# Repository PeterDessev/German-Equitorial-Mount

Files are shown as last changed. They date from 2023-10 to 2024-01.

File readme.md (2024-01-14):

# GEM Driver

An (almost) fully open source German Equitorial Mount currently under development. Publishing of step files for the GEM is under way. The project is based on the Arduino Nano and uses a TMC2209 stepper driver. Amost all parts are either fully 3D-Printable or standard hardware such as metric screws and steel rods.

## Building

Before building initialize and update git submodules, if not already done, with

```zsh
git submodule init
git submodule update
```

Bulding has been tested on Arch linux. To build, run the following.

```zsh
bash quickUpload.sh PORT
```

Where PORT is the arudino's UART port. On linux this is usually `/dev/ttyUSB#`, on windows `com#`.

## TMC Stepper

The main driver of the GEM is a TMC2209 configured over UART. The [TMCStepper library](https://github.com/teemuatlut/TMCStepper/tree/master) was used in the development of the driver, however was stripped down and modified to be more compatable with pure AVR-C, and less reliant on Arduino and the Arduino library. In the future, I would like to completely remove all dependancy on the Arduino Library to simplify building and development.

## Schematic

The schematic was made and can be edited using [KiCad](https://www.kicad.org/). A PCB does not exist yet but is in the works

## Mechanics

Currently the driver is mechanically driven with a NEMA 17 stepper motor mounted on a 100:1 gearbox, though this will be reduced to at least a 25:1 in the future. A 2GT timing belt and two timing pulleys are also used. While printing the pulleys is possible, it is recomended to purchase these to reduce the eccentricity in the drive mechanism, which leads to poor tracking.

### The Worm

The GEM requires a worm gear to drive the tracking mechanism. Printing a worm gear is "possible" depending on the quality of the printer used, however, in most cases it is both easier and produces better results to use a purchased brass worm. In either case, the worm should have a modulus of 0.5 and a bore of at least 6mm to prevent accedentally bending the shaft during assembly or usage. Such worms can be found relativly easily on the internet for around $15, and sometimes come with an accompanying worm drive, which most likely will not be of much use.

## Optics

The GEM also requires a polar scope, which is friction fitted into the gem. The polar scope is the same one used in the SkyWatcher EQ-5, and probably many other mounts, for which replacement parts exist in the usual places on the internet, usually under $100 (I purchased mine off of Amazon for ~$35). Though the polar scope may not be strictly nescessary, since the GEM is much more likely to be limited by the accuracy of the drive mechanism, it makes polar alignment significantly easier, and removes one step in debugging tracking problems.

## Next Steps

Development of the project is planned to continue. Here are the major tasks that still need to be completed, in no particular order:

 - [x] Release CAD files
 - [ ] Move from Atmega to STM32
 - [ ] Create PCB
 - [ ] Add BOM
 - [ ] Create Assembly Instructions
 - [x] Remove Arduino dependancy
 - [x] Release electronics schematic
 - [x] Clean project repo
 - [x] Migrate to a real build system

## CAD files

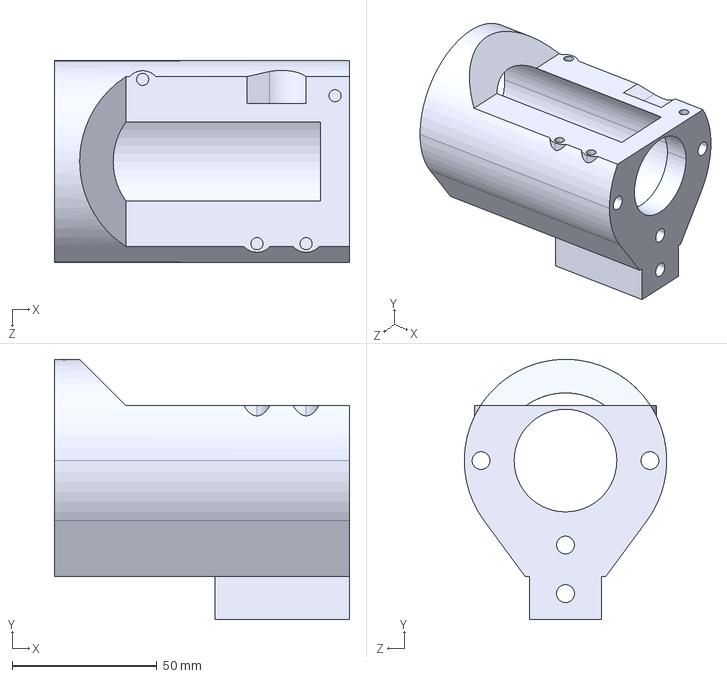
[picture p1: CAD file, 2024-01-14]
cadFiles/step/roll housing.step
102.0 x 90.0 x 70.0 mm

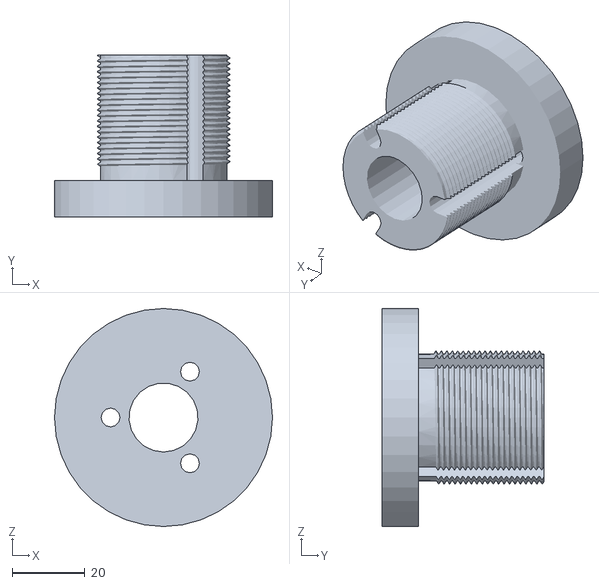
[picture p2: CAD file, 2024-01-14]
cadFiles/stl/roll face slip.STL
60.0 x 44.5 x 60.0

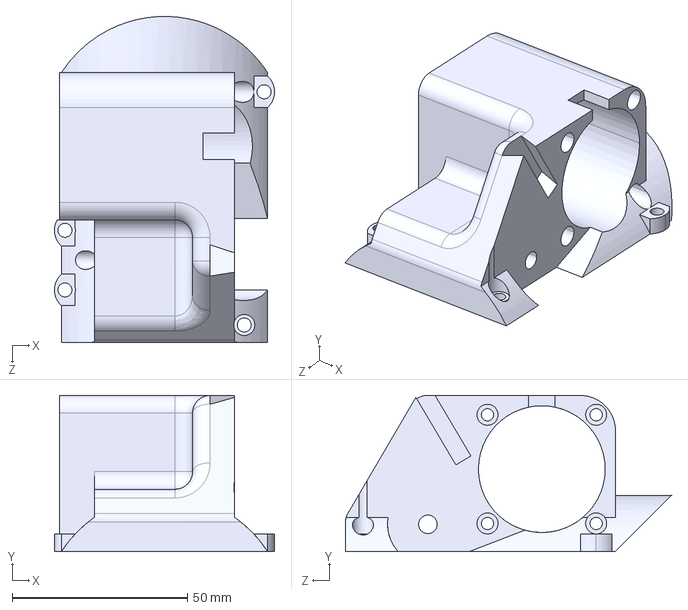
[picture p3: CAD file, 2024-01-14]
cadFiles/step/bridge.step
62.8 x 44.5 x 93.0 mm

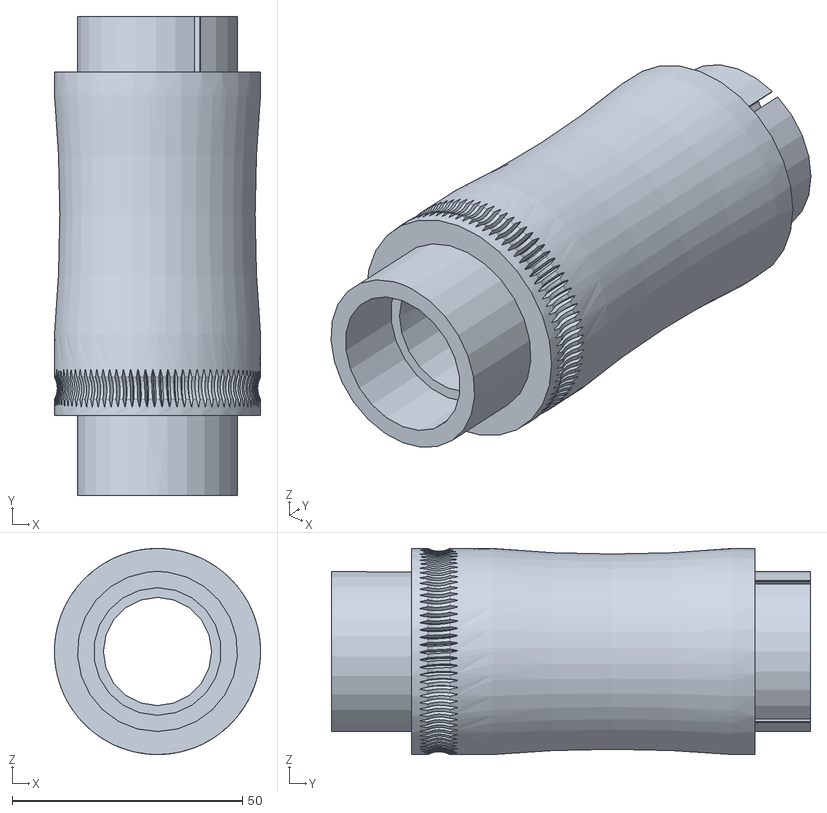
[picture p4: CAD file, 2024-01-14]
cadFiles/stl/roll body.STL
44.8 x 104.0 x 44.8

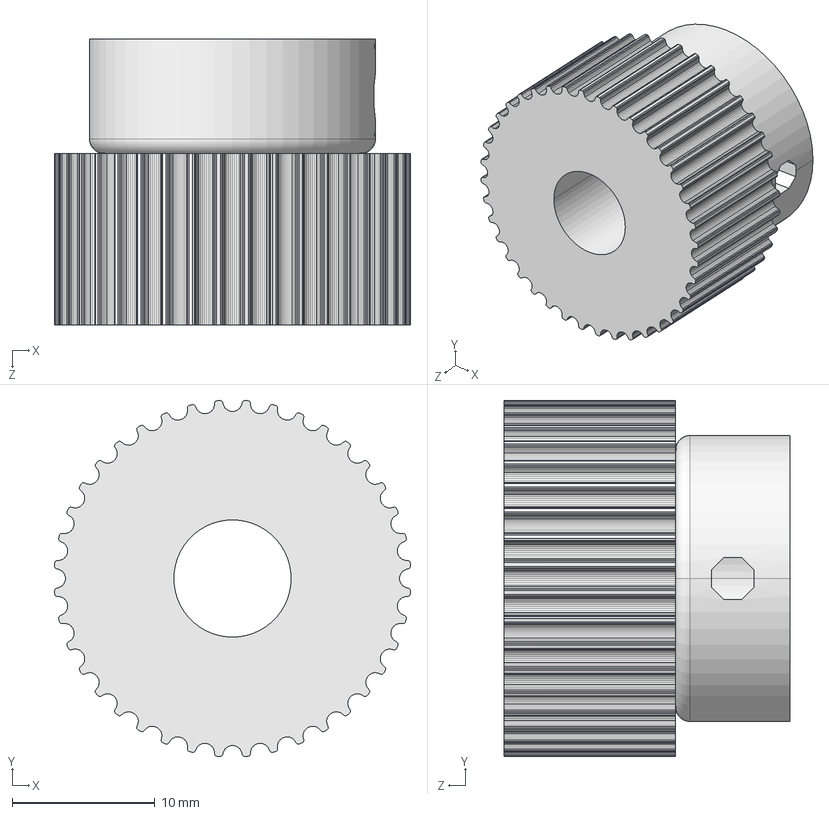
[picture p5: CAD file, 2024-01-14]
cadFiles/step/roll secondary gear.step
24.9 x 24.9 x 20.0 mm

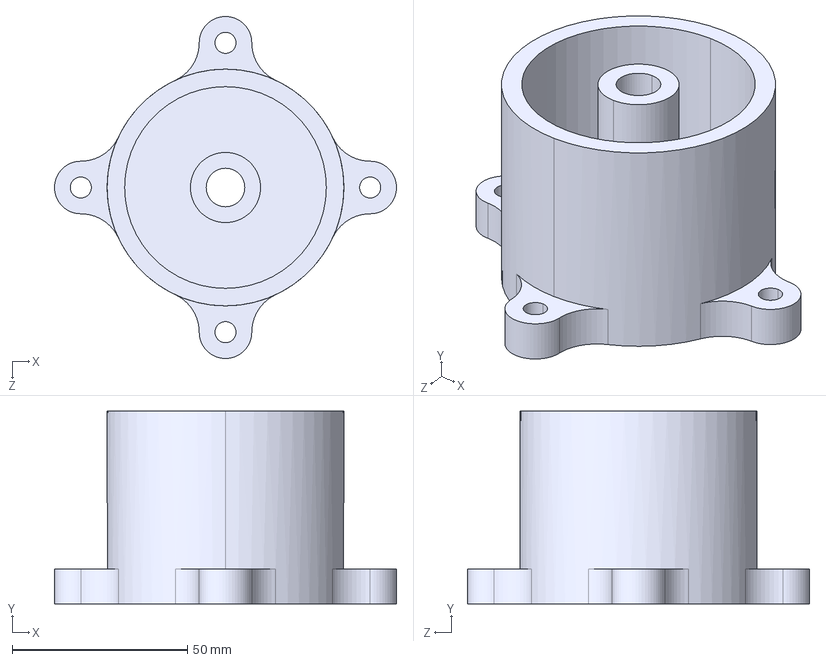
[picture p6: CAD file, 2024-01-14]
cadFiles/step/counterweight base.step
97.5 x 55.0 x 97.5 mm

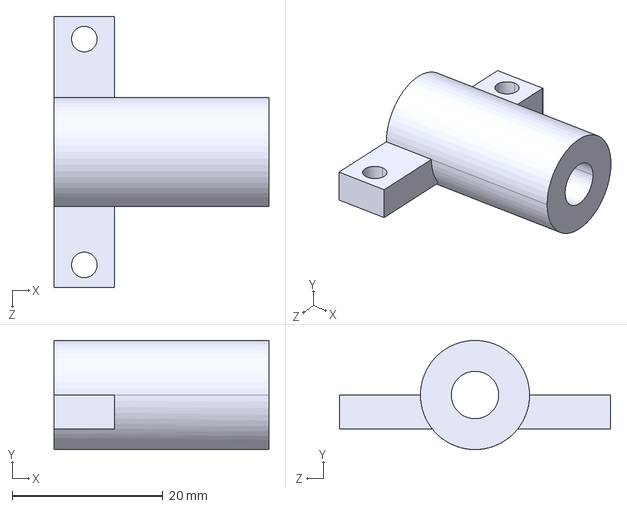
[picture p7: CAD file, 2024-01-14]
cadFiles/step/tilt axle.step
28.5 x 14.5 x 36.0 mm

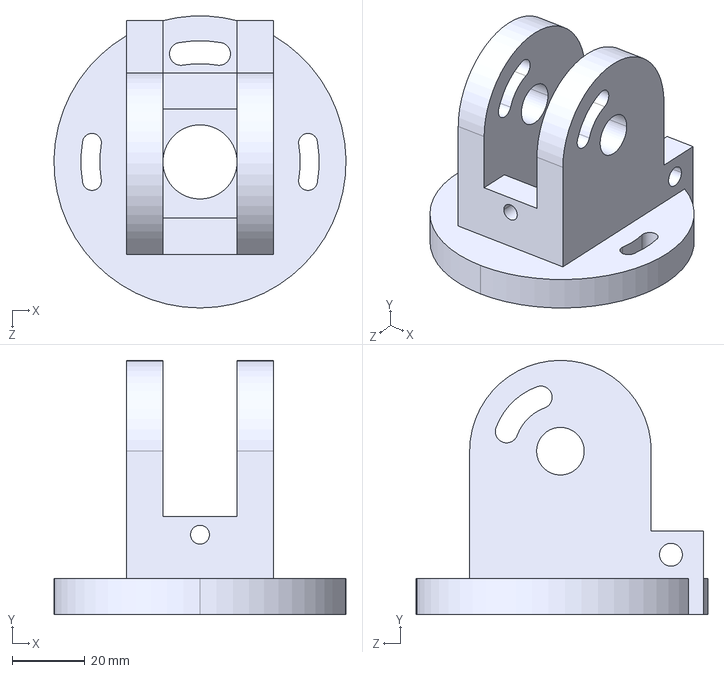
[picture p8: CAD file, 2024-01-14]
cadFiles/step/Az rotar V2.step
80.4 x 70.0 x 80.3 mm

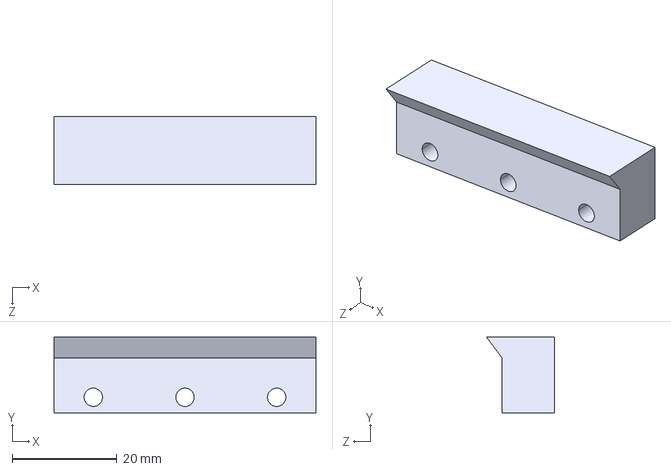
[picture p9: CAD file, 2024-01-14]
cadFiles/step/arca momentary clamp.step
50.0 x 14.5 x 13.0 mm

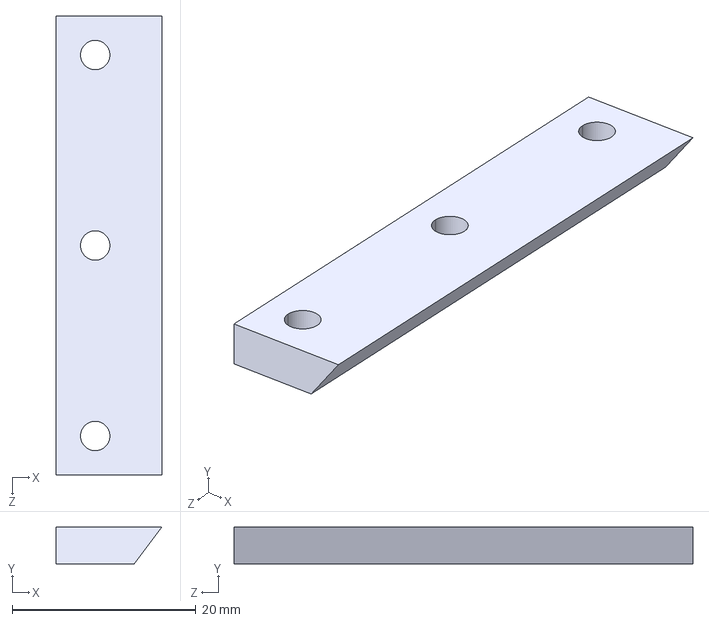
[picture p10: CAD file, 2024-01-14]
cadFiles/step/arca stationary clamp.step
11.5 x 4.00 x 50.0 mm

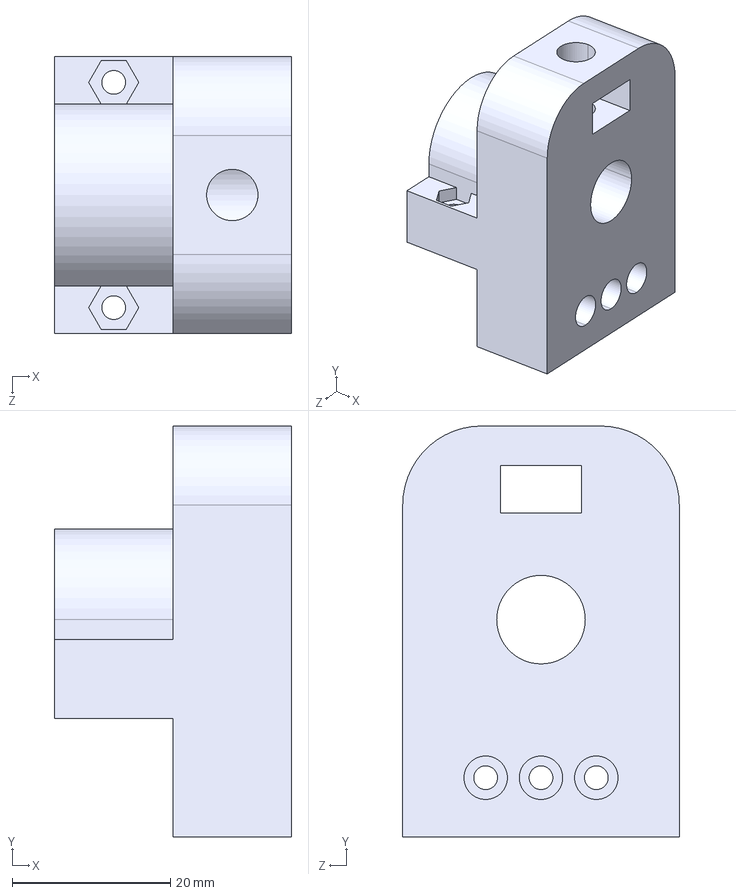
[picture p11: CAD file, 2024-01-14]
cadFiles/step/counterweight mount.step
30.0 x 52.0 x 35.0 mm

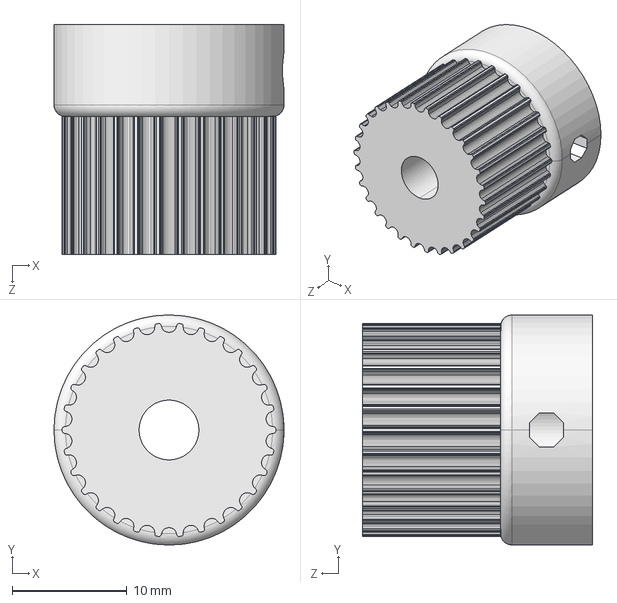
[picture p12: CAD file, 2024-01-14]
cadFiles/step/roll primary gear.step
20.0 x 20.0 x 20.0 mm

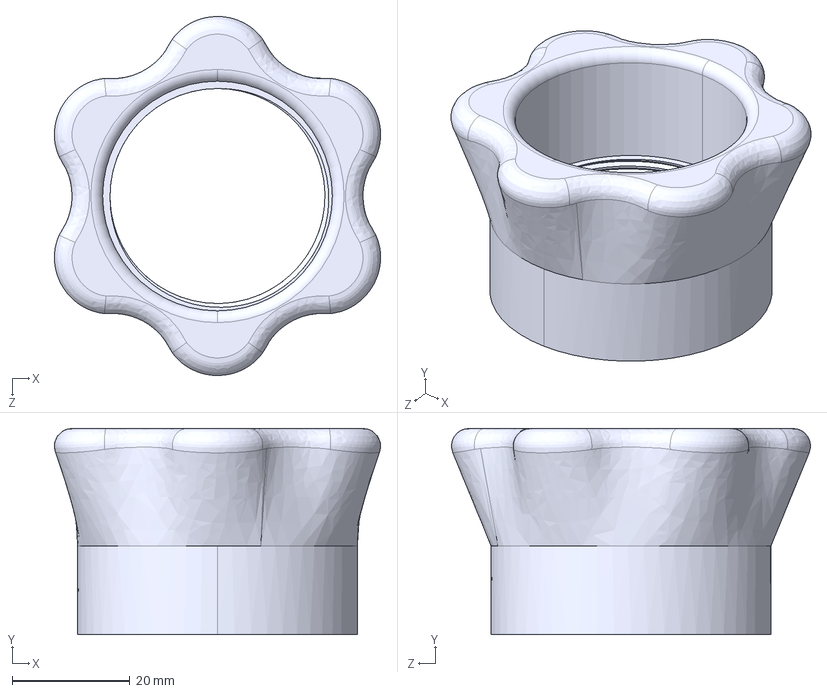
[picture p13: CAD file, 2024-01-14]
cadFiles/step/roll face clamp.step
55.4 x 35.0 x 61.0 mm

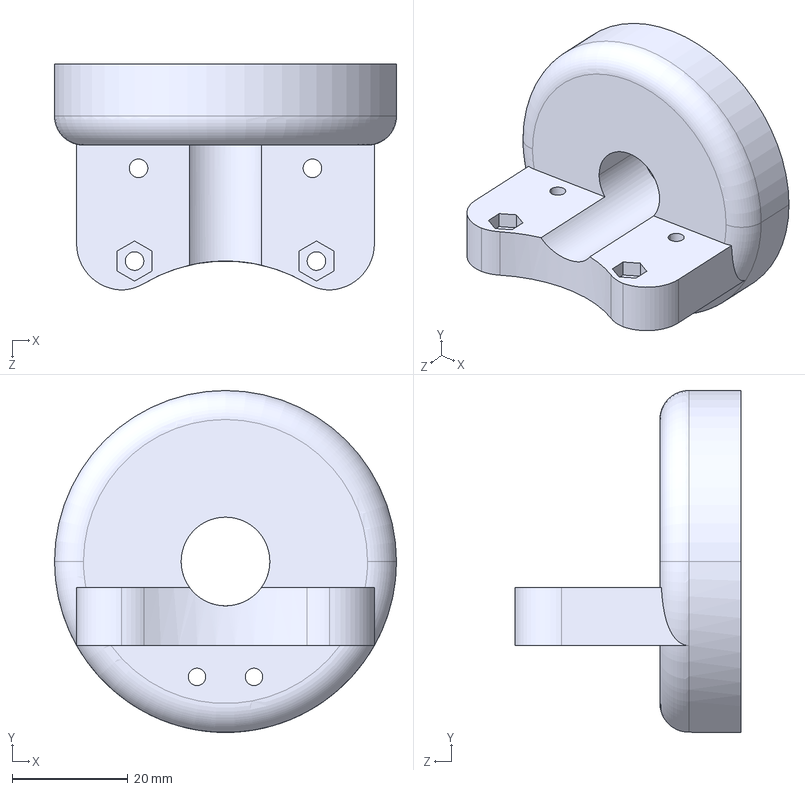
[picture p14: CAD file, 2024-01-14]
cadFiles/step/Tilt base.step
59.0 x 59.0 x 39.0 mm

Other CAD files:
cadFiles/step/motor with gearbox.step
cadFiles/step/bearing standin - DO NOT PRINT.step
cadFiles/step/roll face.step
cadFiles/step/Tilt lower bearing.step
cadFiles/step/Alt rotar.step
cadFiles/step/Clamp Handle.step
cadFiles/step/bearing top.step
cadFiles/step/counterweight cover.step
cadFiles/step/tensioner.step
cadFiles/step/tilt brake.step
cadFiles/step/tripod mount side socket.step
cadFiles/stl/Alt rotar.STL
cadFiles/stl/Az rotar V2.STL
cadFiles/stl/Clamp Handle.STL
cadFiles/stl/Tilt base.STL
cadFiles/stl/Tilt lower bearing.STL
cadFiles/stl/arca momentary clamp.STL
cadFiles/stl/arca stationary clamp.STL
cadFiles/stl/bearing standin - DO NOT PRINT.STL
cadFiles/stl/bearing top.STL
cadFiles/stl/bridge.STL
cadFiles/stl/counterweight base.STL
cadFiles/stl/counterweight cover.STL
cadFiles/stl/counterweight mount.STL
cadFiles/stl/motor with gearbox.STL
cadFiles/stl/roll face clamp.STL
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

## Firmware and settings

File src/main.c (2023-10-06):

#include <avr/interrupt.h>
#include <avr/io.h>
#include <util/delay.h>

#include <stdlib.h>
#include <stdint.h>
#include <stdbool.h>

#include "registers.h"
#include "tmc2209.h"
#include "hwUart.h"
#include "softwareUart.h"

#define MICROSTEPS 32
#define CURRENT 2000
#define EN_PIN 7            // Enable
#define DIR_PIN 3           // Direction
#define STEP_PIN 4          // Step
#define STEP_PORT PORTD     // Step port
#define BAUDRATE 9600
#define DIR 0

#define TRACKDELMS 3
#define TRACKDELUS 70
#define FASTDELUS 8

// Controller Buttons
#define UL_BUTTON_PIN PINB
#define UL_BUTTON_NUM 4
#define UR_BUTTON_PIN PINB
#define UR_BUTTON_NUM 3

// Quickly moves the motor. The motor is stepped with a 
// delay equal to twice delay_ms.
extern inline void fastMove() {
    STEP_PORT |= _BV(STEP_PIN);
    _delay_us(FASTDELUS);
    STEP_PORT &= ~_BV(STEP_PIN);
    _delay_us(FASTDELUS);
}

int main() {
    usartInit(BAUDRATE);

    // Clear DDRD and set all pins to input
    DDRD = 0;

    // Set ports 3, 4, 5, 7 to output
    DDRD |= _BV(DIR_PIN);  // Dir pin output
    DDRD |= _BV(STEP_PIN); // Step pin output
    DDRB |= _BV(5);        // LED pin output
    DDRD |= _BV(EN_PIN);   // Enable pin output

    // Set ports 11, 12 to input
    DDRB &= ~_BV(3); // Controller Button
    DDRB &= ~_BV(4); // Controller Button

    PORTD |= _BV(3); // Set Dir pin to high

    // // Set Software Serial pins to output
    DDRD |= _BV(5);
    DDRD |= _BV(6);

    // Allow in-rush Cap to charge before enabling motor
    PORTD |= _BV(EN_PIN); // Set enable to high
    _delay_ms(2000);
    PORTD &= ~_BV(EN_PIN); // Set enable to low

    softwareUart* raDriverUart = initSoftUart(&DDRD, &PORTD, 5, &DDRD, &PIND, 6);
    tmc2209* raDriver = createDriver(0.11f, 0, raDriverUart);
    
    toff(raDriver, 5);
    rms_current(raDriver, CURRENT); // Set motor RMS current
    microsteps(raDriver, MICROSTEPS);
    pwm_autoscale(raDriver, true);
    tpwmthrs(raDriver, 13); // "Disable" Stealth Chop, enable Spread Cycle
    multistepFilt(raDriver, 1); // Try this one out, see what it does?
    shaft(raDriver, DIR);

    // Automatic Tuning
    // PWM_OFS_AUTO
    // Trigger Run Current
    // STEP_PORT |= _BV(STEP_PIN);
    // _delay_ms(2);
    // STEP_PORT &= ~_BV(STEP_PIN);
    // _delay_ms(2);
    // _delay_ms(140);

    // // PWM_GRAD_AUTO
    // uint16_t rpm = 100;
    // uint16_t gradDel = 300 / rpm;
    // for(uint16_t i = 0; i < 400; i++){
    //     STEP_PORT |= _BV(STEP_PIN);
    //     _delay_ms(gradDel);
    //     STEP_PORT &= ~_BV(STEP_PIN);
    //     _delay_ms(gradDel);
    // }


    while (1) {
        int buttonStat = (~PINB) & (_BV(UL_BUTTON_NUM) | _BV(UR_BUTTON_NUM)); // Get inputs on buttons 

        switch (buttonStat) {
        case _BV(UR_BUTTON_NUM):
            shaft(raDriver, !DIR);
            while((~PINB) & _BV(UR_BUTTON_NUM))
                fastMove();
            shaft(raDriver, DIR);
            break;
        case _BV(UL_BUTTON_NUM):
            while((~PINB) & _BV(UL_BUTTON_NUM))
                fastMove();
            break;
        default: // Move tracker normally
            // PORTB |= _BV(5);
            STEP_PORT |= _BV(STEP_PIN);
            _delay_us(TRACKDELMS * 500);
            _delay_us(TRACKDELUS / 2);
            STEP_PORT &= ~_BV(STEP_PIN);
            // PORTB &= ~_BV(5);
            _delay_us(TRACKDELMS * 500);
            _delay_us(TRACKDELUS / 2);
            break;
        }
    }
    removeDriver(&raDriver);
    removeSoftUart(&raDriverUart);
    return 0;
}

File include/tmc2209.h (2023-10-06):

#pragma once
#pragma pack(push, 1)

#include <stdint.h>

#include "softwareUart.h"

#define GCONF_ADDRESS 0x00
#define IOIN_ADDRESS 0x06
#define SLAVECONF_ADDRESS 0x03
#define FACTORYCONF_ADRESS 0x07
#define VACTUAL_ADDRESS 0x22
#define MSCURACT_ADDRESS 0x6B
#define CHOPCONF_ADDRESS 0x6C
#define PWMCONF_ADDRESS 0x70
#define DRVSTATUS_ADDRESS 0x6F
#define PWMSCALE_ADDRESS 0x71
#define IHOLDIRUN_ADDRESS 0x10
#define TPOWERDOWN_ADDRESS 0x11
#define TPWMTHRS_ADDRESS 0x13

#define TMC2208_SYNC 0x05
#define TMC_WRITE 0x80

#define DEFAULT_HOLD_MULT 0.7f

extern uint16_t bytesWritten;

typedef struct GCONF_t {
    union {
        uint16_t sr : 10;
        struct {
            bool i_scale_analog : 1, internal_rsense : 1, en_spreadcycle : 1,
                shaft : 1, index_otpw : 1, index_step : 1, pdn_disable : 1,
                mstep_reg_select : 1, multistep_filt : 1, test_mode : 1;
        };
    };
} gconf_t;

typedef struct IOIN_t {
    union {
        uint32_t sr;
        struct {
            bool enn : 1, : 1, ms1 : 1, ms2 : 1, diag : 1, : 1, pdn_uart : 1,
                step : 1, sel_a : 1, dir : 1;
            uint16_t : 14;
            uint8_t version : 8;
        };
    };
} ioin_t;

typedef struct SLAVECONF_t {
    union {
        uint16_t sr : 12;
        struct {
            uint8_t slaveaddr : 8;
            uint8_t senddelay : 4;
        };
    };
} slaveconf_t;

typedef struct FACTORY_CONF_t {
    union {
        uint16_t sr;
        struct {
            uint8_t fclktrim : 5, : 3, ottrim : 2;
        };
    };
} factory_conf_t;

typedef struct VACTUAL_t {
    uint32_t sr;
} vactual_t;

typedef struct MSCURACT_t {
    union {
        uint32_t sr : 25;
        struct {
            int16_t cur_a : 9, : 7, cur_b : 9;
        };
    };
} mscuract_t;

typedef struct CHOPCONF_t {
    union {
        uint32_t sr;
        struct {
            uint8_t toff : 4, hstrt : 3, hend : 4, : 4, tbl : 2;
            bool vsense : 1;
            uint8_t : 6, mres : 4;
            bool intpol : 1, dedge : 1, diss2g : 1, diss2vs : 1;
        };
    };
} chopconf_t;

typedef struct PWMCONF_t {
    union {
        uint32_t sr;
        struct {
            uint8_t pwm_ofs : 8, pwm_grad : 8, pwm_freq : 2;
            bool pwm_autoscale : 1, pwm_autograd : 1;
            uint8_t freewheel : 2, : 2, pwm_reg : 4, pwm_lim : 4;
        };
    };
} pwmconf_t;

typedef struct DRV_STATUS_t {
    union {
        uint32_t sr;
        struct {
            bool otpw : 1, ot : 1, s2ga : 1, s2gb : 1, s2vsa : 1, s2vsb : 1,
                ola : 1, olb : 1, t120 : 1, t143 : 1, t150 : 1, t157 : 1;
            uint8_t : 4, cs_actual : 5, : 3, : 6;
            bool stealth : 1, stst : 1;
        };
    };
} drv_status_t;

typedef struct PWM_SCALE_t {
    union {
        uint32_t sr;
        struct {
            uint8_t pwm_scale_sum : 8, : 8;
            int16_t pwm_scale_auto : 9;
        };
    };
} pwm_scale_t;

typedef struct IHOLD_IRUN_t {
    union {
        uint32_t sr : 20;
        struct {
        uint8_t ihold : 5,
                        : 3,
                irun : 5,
                    : 3,
                iholddelay : 4;
        };
    };
} ihold_irun_t;

typedef struct TPOWERDOWN_t {
    uint8_t sr : 8;
} tpowerdown_t;

typedef struct TPWMTHRS_t {
    uint32_t sr : 20;
} tpwmthrs_t;

typedef struct tmc2209_t{
    // Registers
    gconf_t gconf;
    ioin_t ioin;
    slaveconf_t slaveconf;
    factory_conf_t factory_conf;
    vactual_t vactual;
    mscuract_t mscuract;
    chopconf_t chopconf;
    pwmconf_t pwmconf;
    drv_status_t drv_status;
    pwm_scale_t pwm_scale;
    ihold_irun_t ihold_irun;
    tpowerdown_t tpowerdown;
    tpwmthrs_t tpwmthrs;

    // Uart
    softwareUart* uart;

    // Misc
    float rsense;
    float holdMultiplier;
    uint8_t tmc2208Sync;
    uint8_t tmcWrite;
    uint8_t address;
} tmc2209;

tmc2209* createDriver(float rSense, uint8_t uartAddress, softwareUart*  uart);

void defaultSettings(tmc2209* driver);

void removeDriver(tmc2209** driver);

void toff(tmc2209* driver, uint8_t B);

void tpwmthrs(tmc2209* driver, uint32_t B);

void multistepFilt(tmc2209* driver, uint8_t B);

void shaft(tmc2209* driver, uint8_t B);

void rms_current(tmc2209* driver, uint16_t mA);

// void mres(tmc2209 driver, uint8_t B);

void microsteps(tmc2209* driver, uint16_t ms);

void pwm_autoscale(tmc2209* driver, uint8_t B);

#pragma pack(pop)

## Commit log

2023-08-21 removed local arduino dependancy
2023-08-22 Added schematic
    [Main_board.kicad_sch, Schematic.kicad_pcb, Schematic.kicad_sch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]
2023-08-22 Updated with schematic information
2024-01-14 Added Cad Files
    [Alt rotar.STL, Alt rotar.step, Az rotar V2.STL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]
2024-01-14 Updated Schematic
    [logic.kicad_sch]
